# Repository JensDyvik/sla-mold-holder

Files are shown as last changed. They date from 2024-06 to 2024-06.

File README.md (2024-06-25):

# SLA mold holder
*A system for supporting SLA 3D printed injection molds with milled aluminum shells. By Jens Dyvik, for Folkeverkstedet, Deichman public library, Oslo, Norway, June 2024*

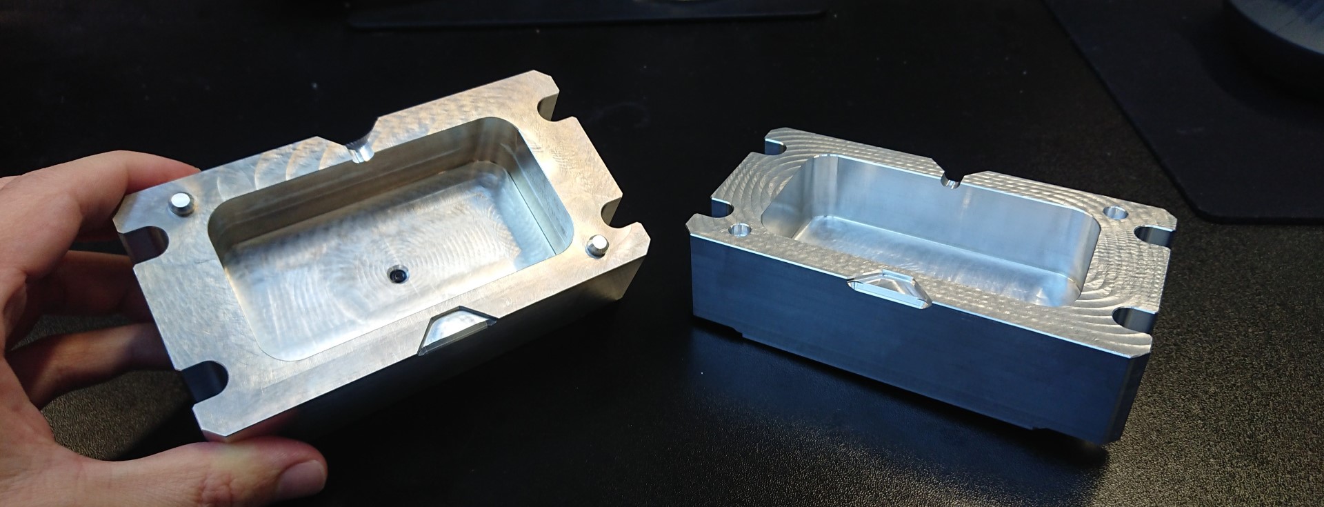
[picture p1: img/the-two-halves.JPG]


### Files for making SLA 3D printed molds

- [Mold blank - STL mesh](https://github.com/JensDyvik/sla-mold-holder/blob/main/stl-files/sla-mold-holder-mold-blank.stl)
- [Mold blank - Step solid](https://github.com/JensDyvik/sla-mold-holder/blob/main/step-files/sla-mold-holder-mold-blank.step)

### Why

SLA 3D printers can make fast and detailed molds for injection molding small series of plastic parts. But the high pressure of injection molding can crack the brittle SLA molds. We have made a simple design for CNC milled two aluminum halves that support the molds during injection to keep them from cracking. These mold holders allows you to use less plastic when 3D printing your molds and inject with higher pressure.

[Folkervekstedet](https://deichman.no/vi-tilbyr/folkeverkstedet_1e2de21d-0716-40b3-a605-43b17ee48b6e) at Deichman has equipment from [Plasticpreneur](https://plasticpreneur.com/) inspired by the [Precious Plastic](https://www.preciousplastic.com/) project for recycling plastic and making new parts. They commissioned Jens Dyvik to design these mold holders so that staff and users of the makerspace can use their Formlabs SLA 3D printer to makes molds, and thereby much easier get started making their own designs with the available equipment or plastic recycling.

We hope that this will inspire more awareness and technical knowhow around plastics recycling in Oslo. And hopefully the 3D printed molds will help recycle more grams of plastic than what is used to resin print the molds.

### How

Download the mold blanks in [STL mesh](https://github.com/JensDyvik/sla-mold-holder/blob/main/stl-files/sla-mold-holder-mold-blank.stl) or [Step solid](https://github.com/JensDyvik/sla-mold-holder/blob/main/step-files/sla-mold-holder-mold-blank.step) format. Import the mold blank into your CAD program and position your design in the mold blank and make a mirror of the mold blank along the XY plane. Make boolean subtractions of the mold blanks minus your design. This should leave a hollow cavity in the mold blanks. You also need to add a "sprue" by subtraction a cylindrical shape where the plastic flows into the mold. Be mindful of "draft angles" and that you need to be able to get the design out of the mold when it has cooled down after injection. Export the two mold halves to your 3D printer program *(PreForm or other)* and print with your SLA 3D printer. Be mindful of resin choice. "Tough" or "High temperature" can make good options, but standard resin can work surprisingly well too.

Once you have cured and removed supports from your mold, place the in the aluminum mold holders and close up with the four finger nuts and carriage bolts. If the fit is too loose you can fill up the gaps with tape or paper. If the fit is too tight you can sand down the molds with sand paper. You can also adjust the tolerance parameters in FreeCAD and 3D print again *(image bellow)* Happy injection molding!

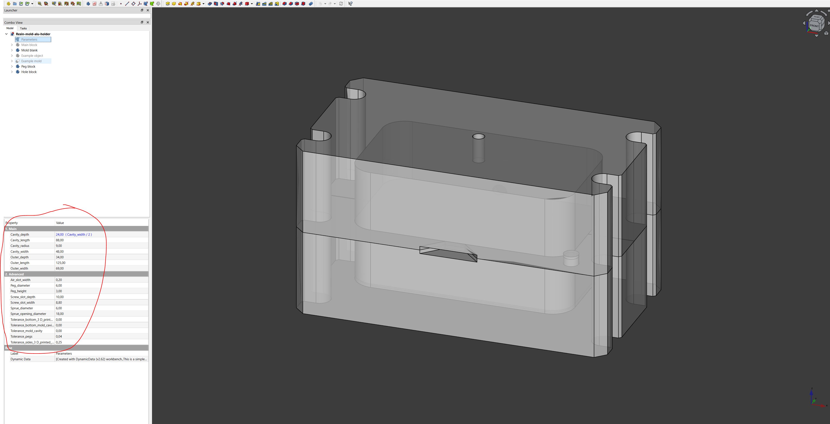
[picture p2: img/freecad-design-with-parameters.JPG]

*The parameters in FreeCAD*

### Pro tips

- Be mindful of shrinkage. Massive volumes of injection molded plastic tends to shrink unevenly when cooling down.
- Be mindful of air gaps. It can be nice to add small channel for air to escape from the molds.
- Be mindful of reducing material use of the molds themselves with shelling and ribs. Example FreeCAD and stl files are in this repo.

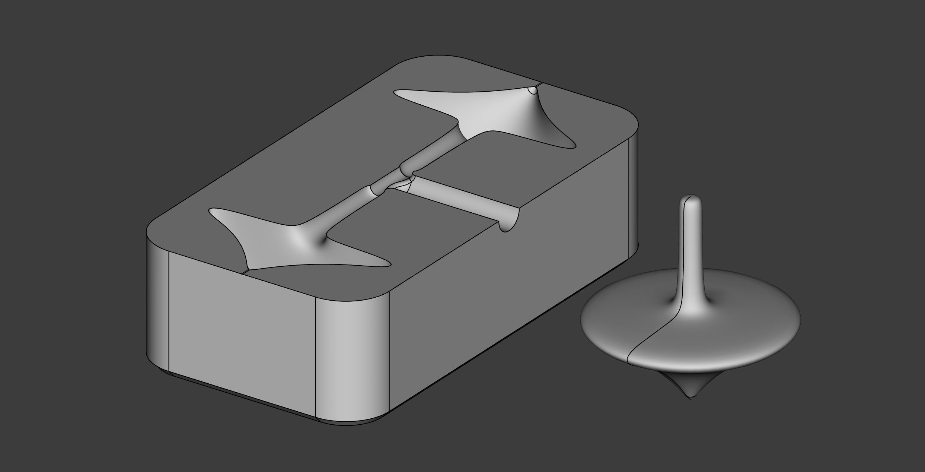
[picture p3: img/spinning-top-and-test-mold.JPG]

*And example mold for a spinning top*

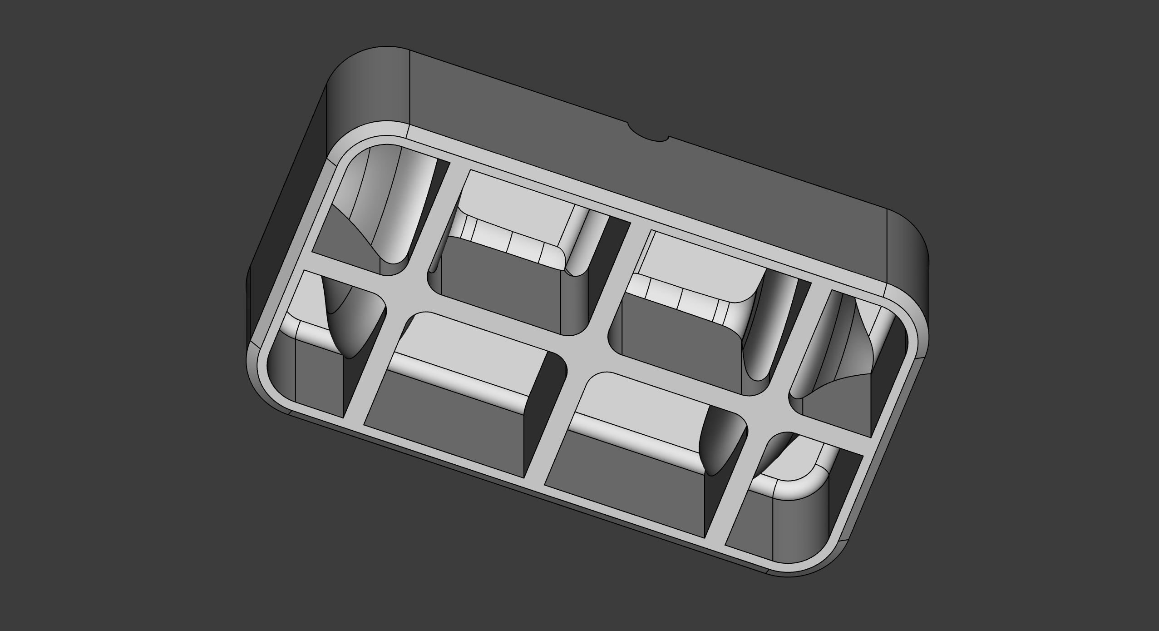
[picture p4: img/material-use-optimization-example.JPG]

*The underside of the example mold, optimized for using less resin material thanks to shelling and ribs*

### Tests

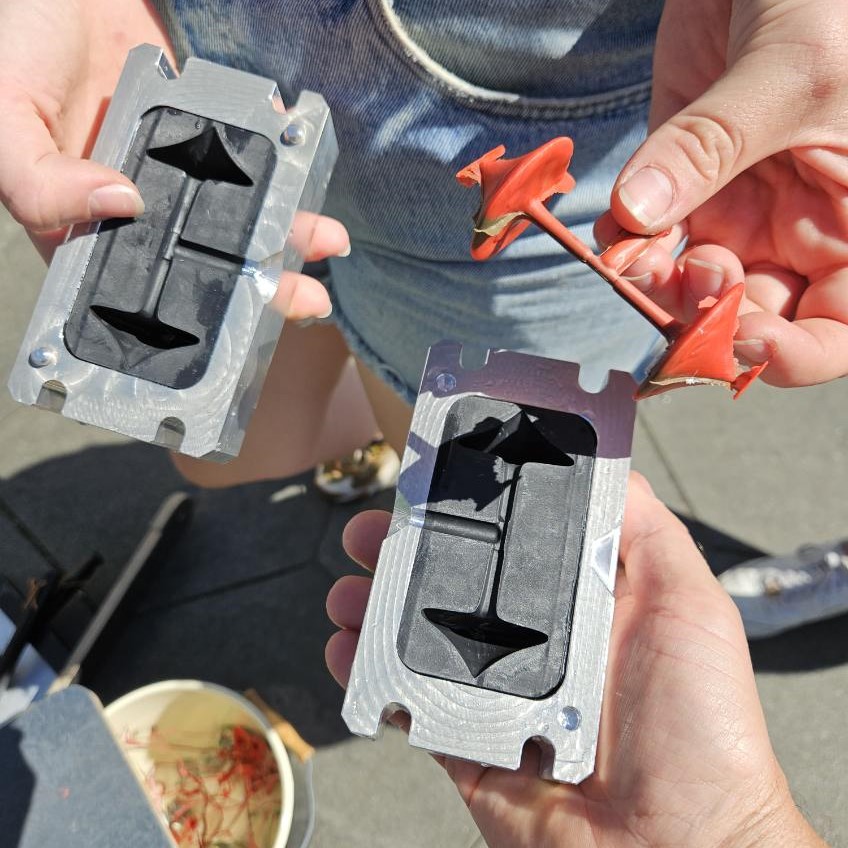
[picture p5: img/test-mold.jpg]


*The printed spinning top test mold and test injection. We made the tolerances for the files for the printed molds tighter to reduce the gaps after this test*

### The making

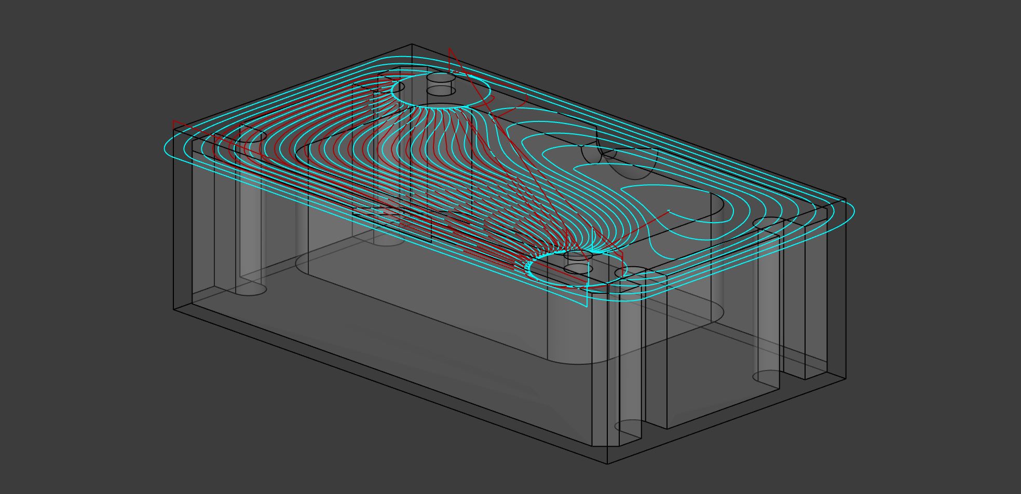
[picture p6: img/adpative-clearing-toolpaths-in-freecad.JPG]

*Adaptive clearing toolpath for CNC milling, made with FreeCAD*

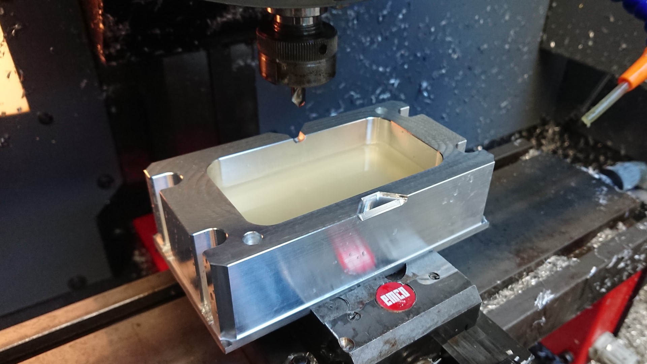
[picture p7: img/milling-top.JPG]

*3 axis milling of the topside done*

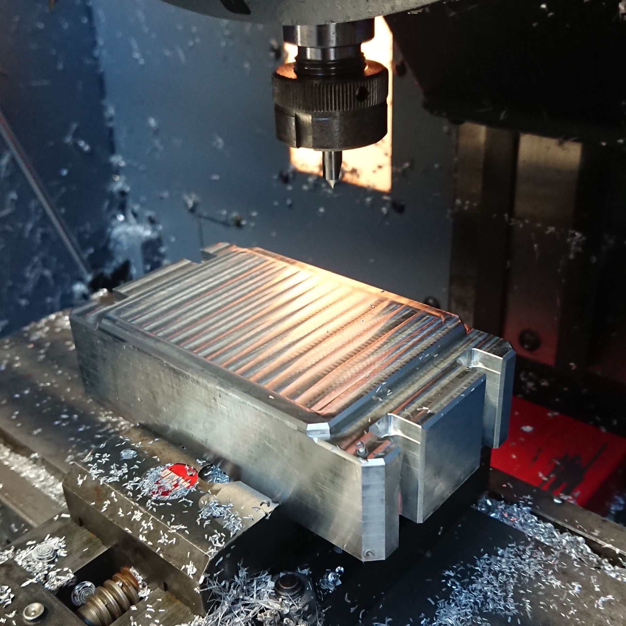
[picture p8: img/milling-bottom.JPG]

*3 axis milling of the bottom side done*

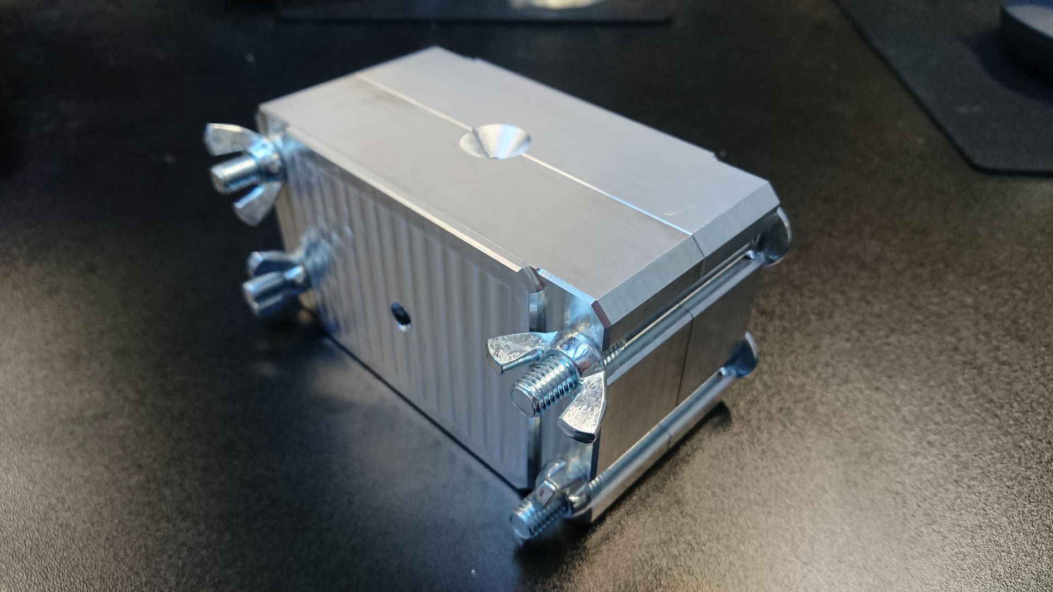
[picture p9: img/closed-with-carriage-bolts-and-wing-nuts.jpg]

*The tow mold holders locked together*

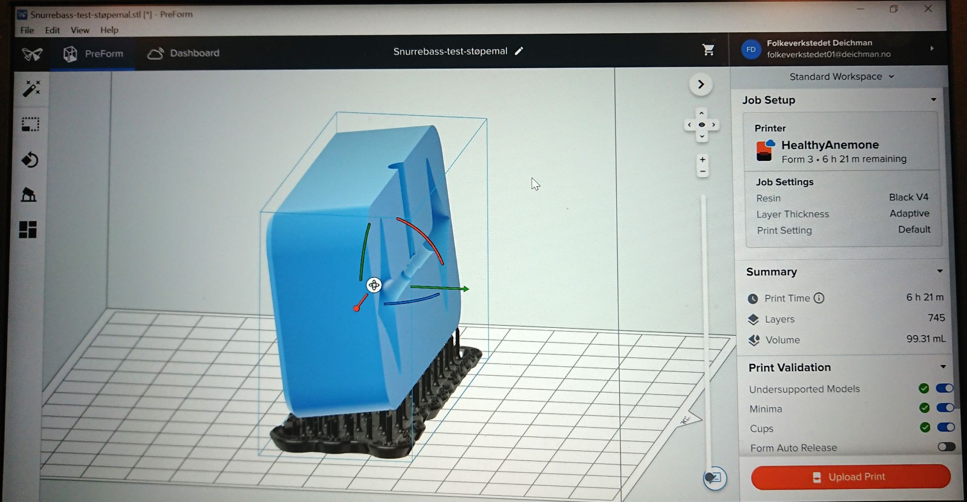
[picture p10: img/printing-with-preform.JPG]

*First test print of a test mold in PreForm*

### Source file

- [FreeCAD design file](https://github.com/JensDyvik/sla-mold-holder/blob/main/freecad-source-files/sla-mold-holder.FCStd)
- [Download link for FreeCAD, free and open source and runs on Linux, Windows and MacOS](https://www.freecad.org/)

### BOM

- 2 pcs: aluminium blanks 40mm x 70mm x 127mm or larger
- 4 pcs: M8 carraige bolt 80mm
- 4 pcs: M8 wing nuts
- SLA 3D printed molds

### Toughts

- The system seems to work well
- Milling the tow mold holders is a lot of work *(30+ different toolpaths, four different milling bits and two sided setup)*
- Sourcing the aluminum blanks from 70mm x 40mm extrusion took some time
- Getting the right tolerance for the resin printed mold sides and bottoms is tricky
- A project like this is at risk of having a negative overall impact on the environment despite its sustainability goal *(lots of aluminum used and lots resin used for printing molds that might not see a lot of use)*
- I hope that the educational and inspirational impact at the Folkeverkstedet makerspace will be large

#### Further reading

- https://formlabs.com/eu/applications/injection-molding/

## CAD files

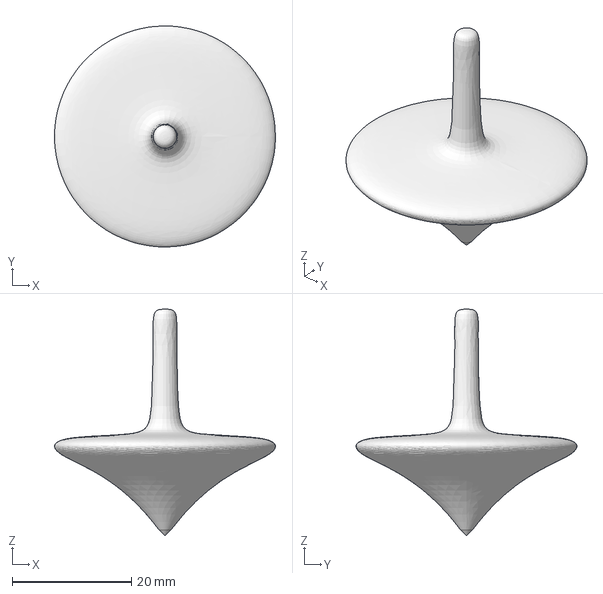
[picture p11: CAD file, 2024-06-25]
freecad-source-files/spinning-top-test-object.FCStd
37.0 x 37.0 x 38.0 mm

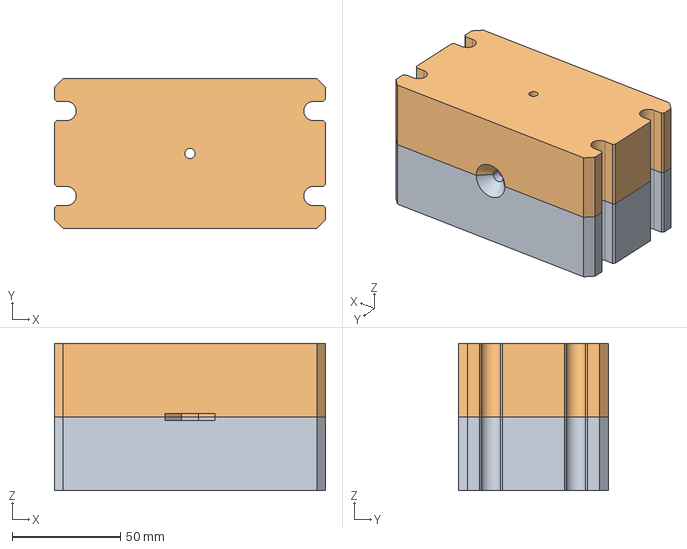
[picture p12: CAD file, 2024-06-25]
step-files/sla-mold-holder.step
125.0 x 69.0 x 68.0 mm

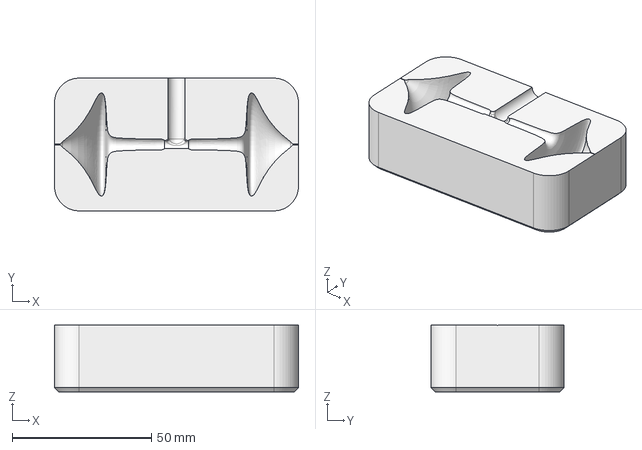
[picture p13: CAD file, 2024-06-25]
freecad-source-files/spinning-top-test-mold.FCStd
87.8 x 47.8 x 24.0 mm

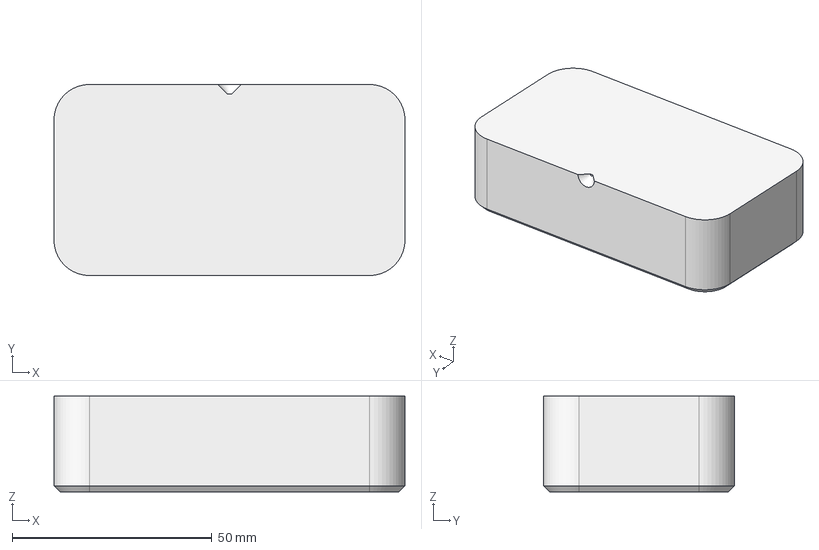
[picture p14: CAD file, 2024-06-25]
step-files/sla-mold-holder-mold-blank.step
87.8 x 47.8 x 24.0 mm

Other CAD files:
freecad-source-files/sla-mold-holder.FCStd
stl-files/sla-mold-holder-mold-blank.stl
stl-files/sla-mold-holder.stl
